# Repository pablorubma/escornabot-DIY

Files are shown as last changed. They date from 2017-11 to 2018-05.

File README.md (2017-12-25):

# AVISO!! En construcción, estos días retocaré muchas cosas aunque lo esencial siempre lo tendrás a mano :P
  
# Escornabot DIY  
  
Material recopilado de [Xoan Sampaiño](https://github.com/xoan), [Rafa Couto](https://github.com/rafacouto), [XDeSIG](https://github.com/xdesig), [Jorge Lobo Martínez](https://github.com/lobotic) y [mgesteiro](https://github.com/mgesteiro)   
  
Web oficial del robot escornabot http://escornabot.com

Vamos a describir uno tras otros todos los pasos a seguir para montar la versión DIY (la de los cablecicos)

# 1. Piezas Impresas3D Necesarias
  
Descripción         | imagen          | archivo         
------------- | ------------- | ------------- 
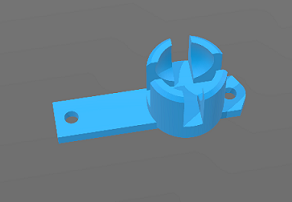
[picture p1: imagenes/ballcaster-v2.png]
ballcaster-v2.stl
Sujeción bola v2| | [ballcaster-v2.stl](archivos-stl/ballcaster-v2.stl)  
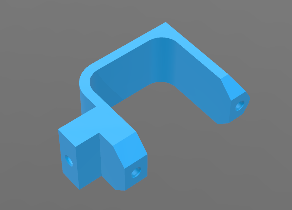
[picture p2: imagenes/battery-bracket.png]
battery-bracket.stl
Sujeción batería| | [battery-bracket.stl](archivos-stl/battery-bracket.stl)  
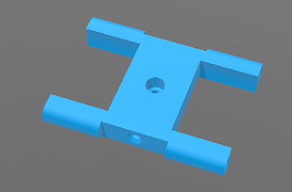
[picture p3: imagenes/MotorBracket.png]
MotorBracket.stl
Sujeción motores| | [MotorBracket.stl](archivos-stl/MotorBracket.stl)  
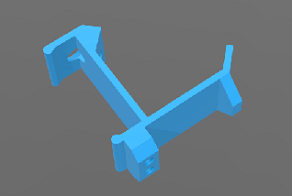
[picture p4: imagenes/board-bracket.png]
board-bracket.stl
Sujeción protoboard 170 puntos| | [board-bracket.stl](archivos-stl/board-bracket.stl)  
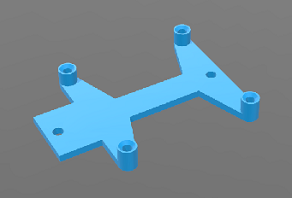
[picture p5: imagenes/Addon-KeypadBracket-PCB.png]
Addon-KeypadBracket-PCB.stl
Sujeción placa botonera| | [Addon-KeypadBracket-PCB.stl](archivos-stl/Addon-KeypadBracket-PCB.stl)  
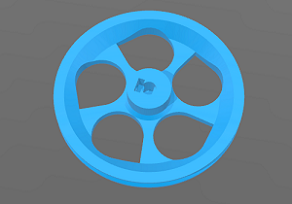
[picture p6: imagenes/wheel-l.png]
wheel-l.stl
Rueda izquierda| | [wheel-l.stl](archivos-stl/wheel-l.stl)  
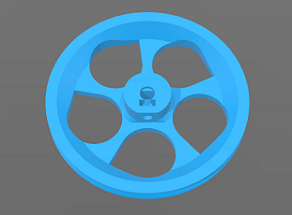
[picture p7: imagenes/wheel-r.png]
wheel-r.stl
Rueda derecha| | [wheel-r.stl](archivos-stl/wheel-r.stl)  

### 1.1 Opcional
  
En mi caso, no monto la pieza "sujeción interruptor". Dejo los cables para conectar macho con hembra y enseñar a los peques la conexión de los cables.

Descripción         | Imagen          | Archivo          
------------- | ------------- | ------------- 
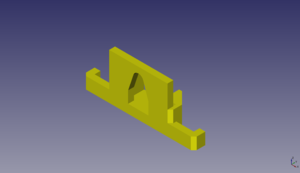
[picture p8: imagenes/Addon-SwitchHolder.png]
Addon-SwitchHolder.stl
Sujeción interruptor| | [Addon-SwitchHolder.stl](archivos-stl/Addon-SwitchHolder.stl)

# 2. Componentes Electrónicos
  
## 2.1. Placa Botonera 

Es la parte más problemática y tienes dos opciones:

### 2.1.1. Placa original totalmente artesanal

Tienes todos los detalles en la web del proyecto [pincha aquí](https://escornabot.com/web/es/content/botonera-audaciuso) 

Placa Original

También la tienes documentada en la  [guía del CFR Ferrol](https://www.edu.xunta.gal/centros/cfrferrol/aulavirtual2/pluginfile.php/18631/mod_resource/content/0/doc/Proxecto_K-KuriBOT_CFR_FERROL.pdf)

### 2.1.2. Versión de [XDeSIG](https://github.com/xdesig)
  
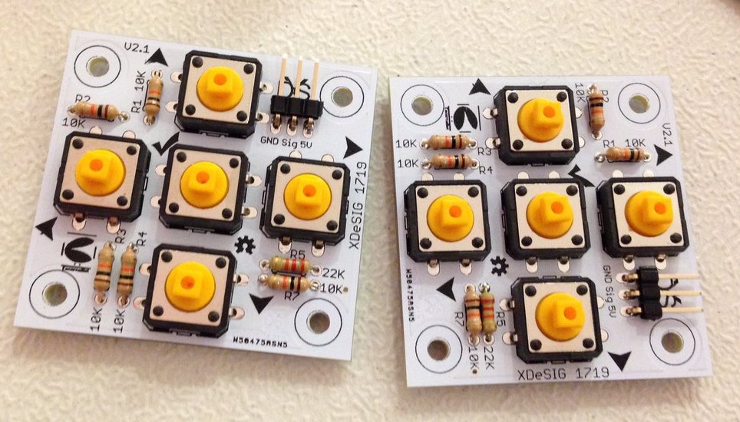
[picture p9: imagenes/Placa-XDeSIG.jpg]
Placa XDeSIG

  
La puedes pedir aquí - [Placa XDeSIG en PCBWay](https://www.pcbway.com/project/shareproject/W50475ASN5_Escorna_bot_2_1_Gerber.html)

Estos son los materiales que necesitas soldar en la placa:

- 5 resistencias 10k
- 1 resistencia 22k
- Pines acodados
- 5 botones 12mm (también puedes poner los pequeños)

### Para esta placa necesitas imprimir una sujeción concreta
  
También tiene carcasa :)
  
Descripción         | Imagen          | Archivo          
------------- | ------------- | ------------- 
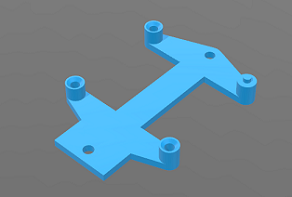
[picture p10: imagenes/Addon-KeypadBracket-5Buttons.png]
Addon-KeypadBracket-5Buttons.stl
Sujeción placa botonera XDeSIG| | [Addon-KeypadBracket-5Buttons.stl](archivos-stl/Addon-KeypadBracket-5Buttons.stl)
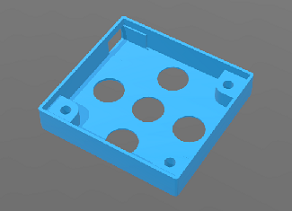
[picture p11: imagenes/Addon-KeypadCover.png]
Addon-KeypadCover.stl
Cubierta botonera XDeSIG| | [Addon-KeypadCover.stl](archivos-stl/Addon-KeypadCover.stl)
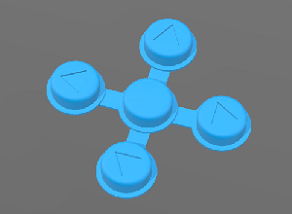
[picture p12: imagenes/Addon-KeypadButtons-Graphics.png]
Addon-KeypadButtons-Graphics.stl
Botones XDeSIG| | [Addon-KeypadButtons-Graphics.stl](archivos-stl/Addon-KeypadButtons-Graphics.stl)
  
__*Recuerda, una vez montada tienes que [comprobar y configurar las lecturas de la botonera](https://escornabot.com/web/es/content/comprobacion-y-configuracion-de-las-lecturas-de-botonera)__

## 2.2. Componentes del cuerpo 

2 – Motores paso a paso **28BY J-48** con “placa” **drive ULN2003**  
2 – Juntas tóricas de **63x60x3** (para las ruedas)  
1 – **Arduino Nano Atmega328** (También puedes usar un Arduino Pro-Mini)  
1 – Zumbador o **Buzzer de 5V**  
1 – **Protoboard** pequeña de **170 puntos**  
1 – **Portapilas** de cuatro unidades para **pilas AA** (no confundir con las AAA que son las finitas)  
20 – Cables arduino macho-hembra (te van a sobrar pero más vale prevenir)  
2 – Cables arduino macho-macho (para la conexión pilas-protoboard)  
16 – Tornillos M3 (a mi me gustan con la punta para destornillador de estrella)  
2 – Tuercas M3 (para las ruedas)  
1 – **Canica de 14mm** (si te gustan las de la carita, busca “bola 14mm smile”)  
  
Si eres curios@ y quieres comprarlos por tu cuenta estoy creando una [lista de componentes](https://github.com/pablorubma/escornabot-DIY/tree/master/componentes)

# 3. Montaje del cuerpo

Puedes consultar la [guía de montaje en la página oficial](https://escornabot.org/wiki/index.php/Gu%C3%ADa_de_montaje_(Brivoi)).

También te sirve de ayuda si montas la [versión Ogaki de abiertocc](https://abierto.cc/shop/#search=ogaki) o la [versión v2.12](https://twitter.com/i/moments/924502947236601856)  

# 4. Cableado de los drivers, buzzer y portapilas

Ya tenemos todo colocado en su sitio, ahora hay que conectar los diferentes componentes con Arduino NANO. Para eso puedes seguir la [guía de cableado](https://escornabot.com/web/es/content/cableado)

# 5. Instalación IDE Arduino y descarga de la programación

Si es la primera vez que utilizas Arduino lo mejor es consultar directamente en la web, [instalar el software (IDE) de arduino](https://www.arduino.cc/en/Guide/Windows)

Las diferentes programaciones las puedes encontrar en el [repositorio de Rafa Couto en GitHub](https://github.com/escornabot/arduino/releases/tag/v1.4.1)

Algunas cosas importantes que debes seleccionar antes de compilar y cargar la programación en tu arduino NANO:

* Selecciona la **placa Arduino NANO** (o la que uses)
* El **procesador** que usa (si es el 164 o 328)
* **Puerto COM del PC** al que lo tienes conectado

# 6. Comprobación de la botonera

Ya lo he comentado antes, pero **este paso se suele olvidar** y **es uno de los que más quebraderos de cabeza causa**. Yo hago la comprobación una vez montado el robot entero, pero tu puedes hacerlo cuando quieras.

[Comprobación y configuración de las lecturas de la botonera](https://escornabot.com/web/es/content/comprobacion-y-configuracion-de-las-lecturas-de-botonera)

Anota los valores de cada botón para editarlos en el archivo **configuration.h**

# 7. A jugar

Si todo ha ido bien, el pequeñajo tiene que empezar a caminar. Cuando te familiarices un poco con Arduino puedes probar a tocar la programación, cambiar los giros, la velocidad, los sonidos del buzzer, añadir sensores, ponerle bluethoot, wifi y todo lo que se te ocurra.

A continuación tienes unos recursos extra :)

# Bluetooth y manejo mediante app android [Jorge Lobo Martínez](https://github.com/lobotic)
  
Puedes ponerle Bluetooth a tu escornabot. Solo necesitas leer el artículo de Jorge en su blog https://ceipmiskatonic.blogspot.com.es/2015/07/usando-el-escornabot-por-bt.html

# MUWI uso mediante Wifi con módulo ESP-01 [mgesteiro](https://github.com/mgesteiro) 
  
Con la placa escornabot v 2.12 va muy bien, con la versión DIY todavía no he probado.

De todos modos, os dejo el enlace al repositorio de Miguel donde podeis encontrar toda la información para que lo tengáis a mano. https://github.com/escornabot/esp-muwi

# Guías y manuales
  
Guía de montaje del CFR Ferrol, es en la que me basé para montar mi primer escornabot. Tienes instrucciones detalladas para montar la botonera - [Guía montaje CFR Ferrol](https://www.edu.xunta.gal/centros/cfrferrol/aulavirtual2/pluginfile.php/18631/mod_resource/content/0/doc/Proxecto_K-KuriBOT_CFR_FERROL.pdf)

Listado completo de materiales necesarios, web original escornabot. Todos los componentes que te haran falta para poner al pequeñajo a caminar - [Listado materiales](http://escornabot.org/wiki/index.php/Lista_de_materiales_(Brivoi))

Guía de montaje sin incluir ensamblaje de botonera, web original escornabot - [Guía montaje](http://escornabot.org/wiki/index.php/Gu%C3%ADa_de_montaje_(Brivoi))

Como comprobar la lectura de la botonera para luego modificar los valores en el archivo "configuration.h" - [Comprobación botonera](https://escornabot.com/web/es/content/comprobacion-y-configuracion-de-las-lecturas-de-botonera)

Diferentes versiones de Rafa Couto realizadas hasta ahora [Versiones arduino para escornabot](https://github.com/escornabot/arduino/releases)  

# Recursos y materiales

En la wiki del proyecto oficial tienes un apartado dedicado a recursos donde puedes encontrar actividades o tableros para escornabot [Recursos Wiki Oficial](http://escornabot.org/wiki/index.php/Recursos)
  
Un imprescindible es el Blog de [Jorge Lobo Martínez](https://github.com/lobotic), donde comparte las actividades que hace en clase. Te dejo enlace a la sección donde trata cosas de escornabot pero revisa el blog completo porque mola mucho - [Blog Lobotic](http://ceipmiskatonic.blogspot.com.es/search/label/Escornabot)
  
Puedes disfrazar a tu pequeñajo [Disfraz Escornabot](https://github.com/pablorubma/escornabot-DIY/tree/master/disfraces)

# Para solucionar dudas y problemas

Si tienes cualquier duda puedes abrir un tema en el grupo creado en google y entre todos te ayudaremos :)
https://groups.google.com/forum/#!forum/escornabot_users

## Bienvenid@ al lado escornabot de la fuerza muahahaha

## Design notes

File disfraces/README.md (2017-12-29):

# Quiero mi disfraz!!

El origen de todo esto viene de [@mininacheshire](https://twitter.com/escornabot/status/568520109033009152) y del [blog de Lobotic](http://ceipmiskatonic.blogspot.com.es/2016/01/disfraces-para-escornabot-brivoi.html)

# Material necesario
* Goma eva
* Tijeras o cuter
* Regla
* Pegamento
* Folios
* Pinturas
* Ojos molones
* Cualquier objeto que resulte útil
  
## Manos a la obra
Un A3 de goma eva mide 30cm de ancho y da de sobra para cubrir el robot de lado a lado. Los 42 cm de largo permite cortar 6 tiras de 7 cm en cada plancha. Yo hago los cortes con cúter, pero si van a trabajar los peques con tijeras mucho mejor 🙂

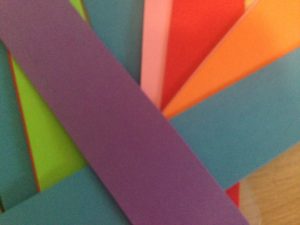
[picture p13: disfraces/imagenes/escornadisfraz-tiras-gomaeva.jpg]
escornadisfraz-tiras-gomaeva


# Disfrazando la versión DIY
Para simplificar usaremos las piezas para fijar el disfraz, en concreto la bola y la placa.
  
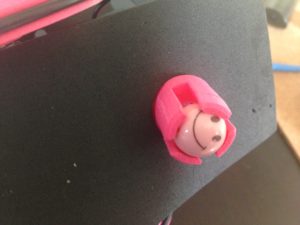
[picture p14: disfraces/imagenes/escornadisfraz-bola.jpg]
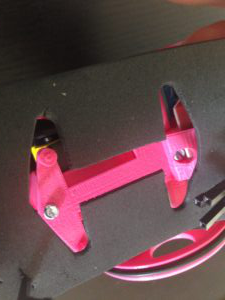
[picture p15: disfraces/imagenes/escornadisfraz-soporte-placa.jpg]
 
  
Las propias piezas nos van a servir de plantilla para cortar su silueta. Colocando la tira sobre el robot puedes calcular donde quieres que quede la tira, en mi caso los puse para que se quedara el corte en la parte de la bola:
  
## Cableado
Haremos unos agujeros para pasar los cables de las baterías y los que conectan a la placa.
  
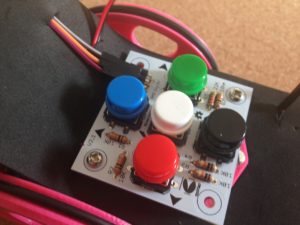
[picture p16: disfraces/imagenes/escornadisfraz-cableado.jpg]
escornadisfraz-cableado
  
  
## Buzzer o altavoz
El buzzer o zumbador lo podemos pinchar directamente en la plancha y utilizarlo de nariz.  Por la parte trasera se conectan los cables sin problema quedando bastante sujeto.
  
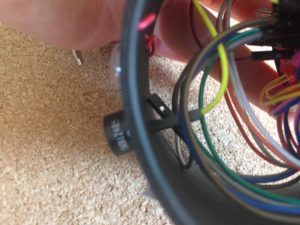
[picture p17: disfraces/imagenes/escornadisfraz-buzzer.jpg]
escornadisfraz-buzzer
  
  
## Ojos
Yo no puedo evitar usar estos ojos pero cada uno debe utilizar su imaginación. Para las cejas he utilizado el mismo cable de arduino haciendo dos agujeros donde anclar los extremos, después puedes darle la forma que quieras.
  
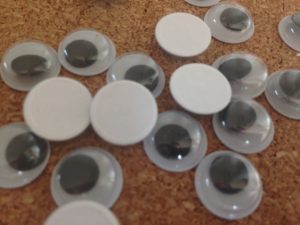
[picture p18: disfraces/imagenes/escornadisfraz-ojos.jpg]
escornadisfraz-ojos
  
    
## Boca
Buscando un poco por Internet tienes un montón de imágenes con bocas para imprimir, recortar y pegar.
  
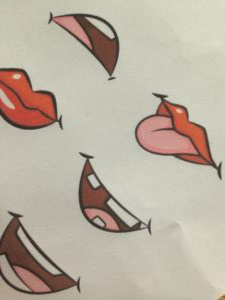
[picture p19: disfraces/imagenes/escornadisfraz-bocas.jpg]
escornadisfraz-bocas
  
    
## Cuerpo
Utiliza trozos de goma eva para adornar el cuerpo, folios pintados o cualquier objeto que puedas pegar y quede molón.
  
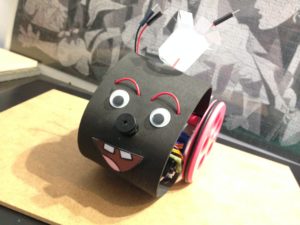
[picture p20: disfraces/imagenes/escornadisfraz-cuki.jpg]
escornadisfraz-cuki
  
    
# Disfrazando la versión 2.12
En este caso hay que tener en cuenta que la placa es rectangular y más grandota. Como en la anterior uso las propias piezas para anclar la goma eva.
  
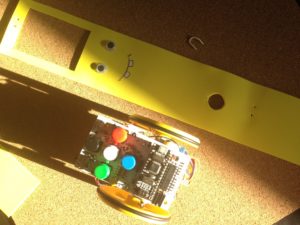
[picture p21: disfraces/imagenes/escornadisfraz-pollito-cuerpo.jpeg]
escornadisfraz-pollito-cuerpo
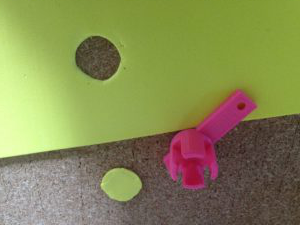
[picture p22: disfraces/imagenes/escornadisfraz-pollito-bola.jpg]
escornadisfraz-pollito-bola
   
    
Al no tener cables necesitas menos trozo de largo para cubrir el robot entero. Yo he utilizado ese sobrante para fabricarle una colita usando un cable como fijación para poder quitar y poner con facilidad.
  
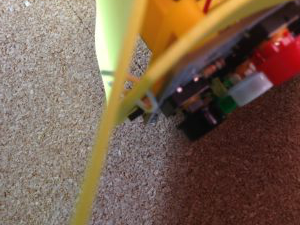
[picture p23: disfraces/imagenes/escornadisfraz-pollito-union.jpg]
escornadisfraz-pollito-union
  
    
Ya tienes una base sobre la que trabajar, ahora imaginación al poder.
  
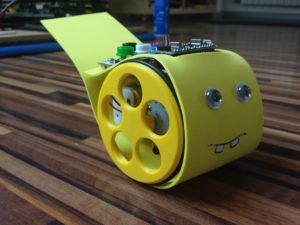
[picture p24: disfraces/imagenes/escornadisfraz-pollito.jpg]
escornadisfraz-pollito
  
    
# Otros ejemplos
En la wiki oficial tienes muchos ejemplos que te pueden dar ideas, te dejo enlace a [máscaras Escornabot](http://escornabot.org/wiki/index.php/Recursos#M.C3.A1scaras)

También este video de Youtube del [CEIP Avion](https://www.youtube.com/watch?v=MtaqqE0XVQg)

O este otro de [Jorge Alba](https://twitter.com/_jorgealba/status/941775330112614401)

# Caretas [Lobotic](https://github.com/lobotic/Escornabot/tree/master/3D) para impresión 3D

[Elefante](https://www.thingiverse.com/thing:2722321)  
[león](https://www.thingiverse.com/thing:2731368)  
[Mono](https://www.thingiverse.com/thing:2735957)  
  
Prueba, juega, crea y sobre todo…
  
# Comparte tu disfraz!

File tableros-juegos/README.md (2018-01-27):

# Material didáctico para usar con [escornabot](http://escornabot.com)

Material recopilado de la [wiki oficial](http://escornabot.org/wiki/index.php/Recursos)

# Tableros  

## Tablero casillas blancas y oficial escornabot

El tablero con casillas blancas es muy interesante si le ponemos bolsas tipo zip cortadas en cada casilla y las utilizamos para meter tarjetas personalizadas.

Tienes en la parte inferior las tarjetas con recorridos, recortadas van eligiendo al azar un recorrido.

Tablero A-3         | Archivo SVG          | Archivo PDF         
------------- | ------------- | -------------              
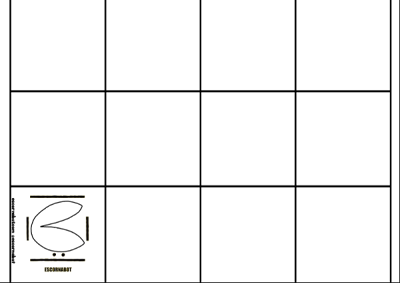
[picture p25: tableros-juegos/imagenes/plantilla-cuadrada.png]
  | [Plantilla cuadrados formato .SVG](https://drive.google.com/file/d/0B32DBGno8hnobk51LXhJUHp0Vlk/view) | [Plantilla cuadrados formato .PDF](https://drive.google.com/file/d/0B32DBGno8hnodjZWVXVJTGdiY0k/view)  
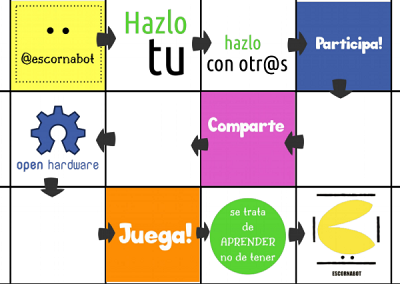
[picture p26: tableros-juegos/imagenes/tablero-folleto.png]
 | [Tablero folleto formato .SVG](https://drive.google.com/file/d/0B32DBGno8hnoeld1VlFjakIzUFE/view?usp=drive_web) | [Tablero folleto formato .PDF](https://drive.google.com/file/d/0B32DBGno8hnoM1pBOEhCa0lFTjg/view) 

## Tablero números

Puedes jugar tirando un dado y que busquen la casilla, realizando sumas simples... Edita el tablero para complicarlo.

Otro juego divertido son las carreras. Es para dos personas, cada uno con un escornabot y fuera del tablero. Se lanza un dado, como los números se repiten el objetivo es que alcancen la primera casilla que vean.

Tablero A-3         | Archivo SVG          | Archivo PDF         
------------- | ------------- | -------------   
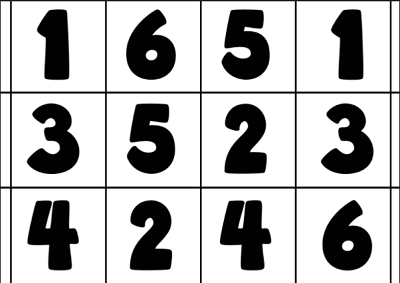
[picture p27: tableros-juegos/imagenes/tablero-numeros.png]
 | [Tablero Números formato .SVG](https://drive.google.com/file/d/0B32DBGno8hnoTDlCNWl0N3ZRdGc/view) | [Tablero Números formato .PDF](https://drive.google.com/file/d/0B0UX14YozB7jTno0dTlkeHpnVVFTNGMzaFpuelZmNlhidkNF/view) 

## Tablero condicional

Se debe llegar desde la casilla inferior izquierda con el triángulo verde hasta la casilla inferior derecha cumpliendo las condiciones de las casillas. La casilla con el aspa roja no se puede pisar, del mismo modo que la azul ya que se caería al agua.

Tablero A-3         | Archivo SVG          | Archivo PDF         
------------- | ------------- | -------------   
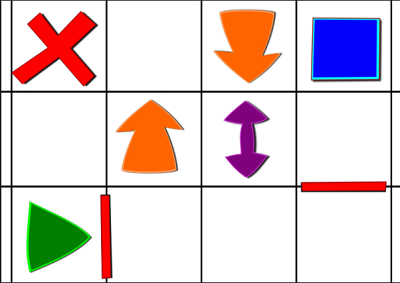
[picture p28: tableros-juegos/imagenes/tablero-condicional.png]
 | [Tablero condicional formato .SVG](https://drive.google.com/file/d/0B32DBGno8hnocW1KQ2dnUHFKVzg/view) | [Tablero condicional formato .PDF](https://drive.google.com/file/d/0B32DBGno8hnoalZfUDlqZjEya1U/view)  

## Tablero figuras geométricas

Se pueden recortar las figuras interiores o cambiar de color para que l@s peques primero hagan la composición del tablero, luego juegan combinando colores y formas geométricas. Puedes crear dos dados, uno contiene colores y otro las formas geométricas.

Tablero A-3         | Archivo SVG          | Archivo PDF         
------------- | ------------- | -------------   
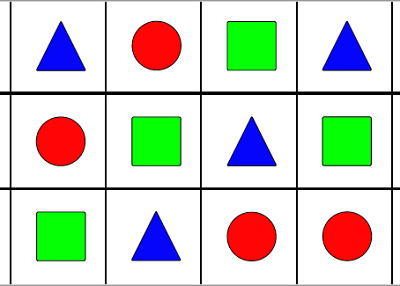
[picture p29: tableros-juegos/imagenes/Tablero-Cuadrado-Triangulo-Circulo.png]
  | [Tablero-Cuadrado-Triangulo-Circulo.svg](archivos/Tablero-Cuadrado-Triangulo-Circulo.svg) | [Tablero-Cuadrado-Triangulo-Circulo.pdf](archivos/Tablero-Cuadrado-Triangulo-Circulo.pdf)  

## Tableros alfabeto

Para trabajar las letras con animalicos :)

Tablero A-3         | Archivo SVG          | Archivo PDF         
------------- | ------------- | -------------   
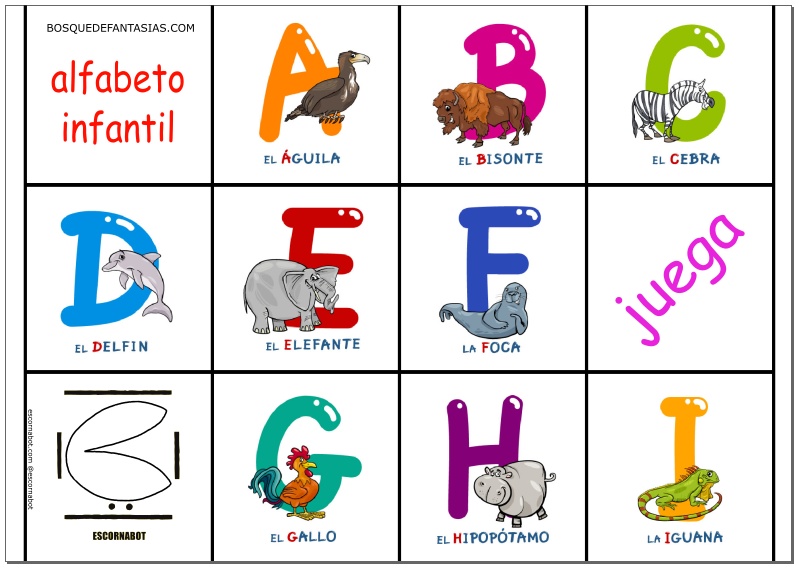
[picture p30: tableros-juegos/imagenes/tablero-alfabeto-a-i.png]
  | [tablero-alfabeto-a-i.svg](archivos/tablero-alfabeto-a-i.svg) | [tablero-alfabeto-a-i.pdf](archivos/tablero-alfabeto-a-i.pdf)  
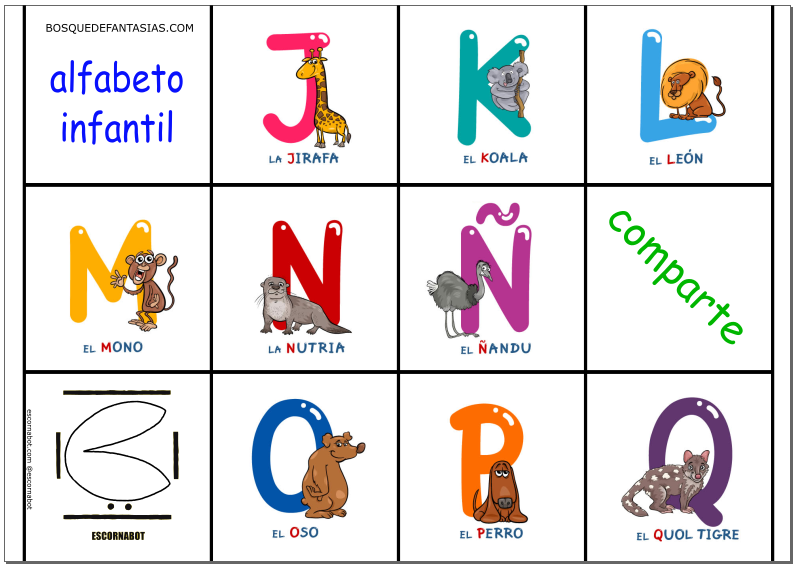
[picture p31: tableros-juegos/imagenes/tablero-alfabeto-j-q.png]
  | [tablero-alfabeto-j-q.svg](archivos/tablero-alfabeto-j-q.svg) | [tablero-alfabeto-j-q.pdf](archivos/tablero-alfabeto-j-q.pdf)  
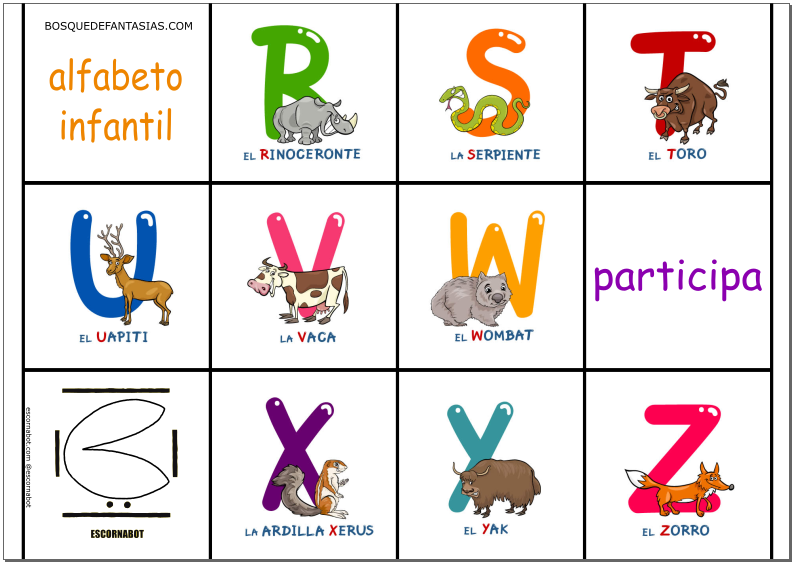
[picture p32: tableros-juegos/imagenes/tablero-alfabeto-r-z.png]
  | [tablero-alfabeto-r-z.svg](archivos/tablero-alfabeto-r-z.svg) | [tablero-alfabeto-r-z.pdf](archivos/tablero-alfabeto-r-z.pdf)  

## Tablero triangular

Tablero A-3         | Archivo SVG          | Archivo PDF         
------------- | ------------- | -------------   
Para usar la plantilla triangular debes cambiar la programación para que los grados en los giros se adapten al dibujo, el robot debe ir por las líneas y llegar a los vértices de los triángulos

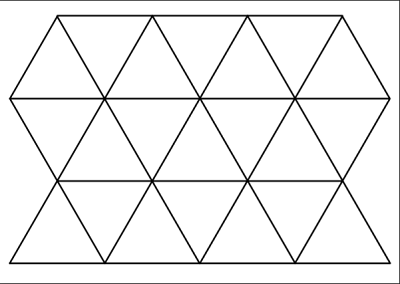
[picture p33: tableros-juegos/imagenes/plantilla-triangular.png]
  | [Plantilla triangular formato .SVG](https://drive.google.com/file/d/0B32DBGno8hnoSEkyN3VRM1I0Rmc/view) | [Plantilla triangular formato .PDF](https://drive.google.com/file/d/0B32DBGno8hnod1pXVzdfVG54VnM/view)  

## Tablero escritores gallegos
  
Tableros A-4         | Archivo SVG          | Archivo PDF         
------------- | ------------- | -------------       
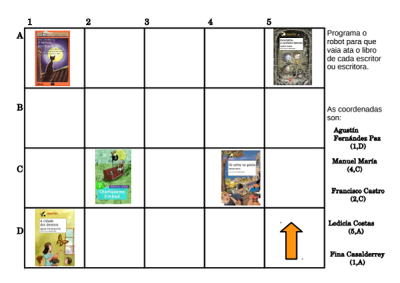
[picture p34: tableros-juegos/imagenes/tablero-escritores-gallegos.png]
 | | [Tablero escritores gallegos formato .PDF](https://drive.google.com/file/d/0B5m90BTAG1QYSExtNWdBNjVuU0E/view)  

## Tarjetas

Tarjeta         | Archivo            
------------- | -------------       
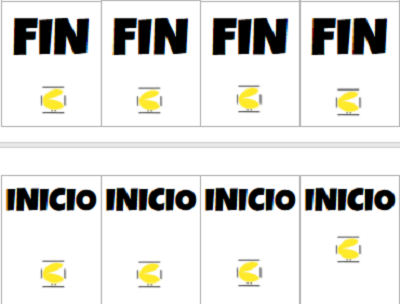
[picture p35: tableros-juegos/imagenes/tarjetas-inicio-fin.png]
 | [Tarjetas inicio-fin formato Word](https://docs.google.com/document/d/12gfkgnx5Rgb8NKzSXDHQ7-2KmUop8931cPN26ciuWcE/edit) 
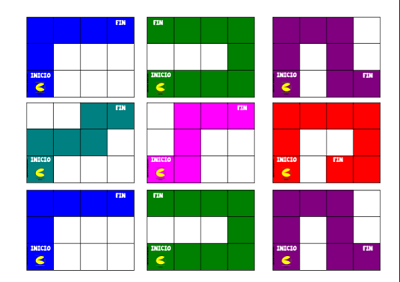
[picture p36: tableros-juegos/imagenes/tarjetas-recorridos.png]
 | [Tarjetas recorridos formato .PDF](https://drive.google.com/file/d/0B0UX14YozB7jTGZ3d1dYSGNsSkJZU0Fqd1BTMjJCMWdHVGRB/view) 
 | [Tarjetas frutas formato Word](https://docs.google.com/document/d/1xnoPbf6wEXKz65S-1-KflOl4RJz2JpOLmkt9J7G1E6k/edit)  
 | [Tarjetas ecosistemas formato .PDF](http://escornabot.org/wiki/images/f/f7/Ecosistemas.pdf)
  
## Dados

[Cuerpos Geométricos para utilizar como dados](https://drive.google.com/file/d/0B0UX14YozB7jc0IyU1Rfb01kR3M/view)

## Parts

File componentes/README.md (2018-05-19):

### IMPORTANTE - Cada uno es responsable de lo que compre esto simplemente es una orientación

## Teneis los componentes necesarios para montar un escornabot en el [repositorio version DIY](https://github.com/pablorubma/escornabot-DIY/blob/master/README.md)

2 – Motores paso a paso 28BY J-48 con “placa” drive ULN2003  
2 – Juntas tóricas de 63x57x3 (para las ruedas)  
1 – Arduino Nano Atmega328 (También puedes usar un Arduino Pro-Mini)  
1 – Zumbador o Buzzer de 5V  
1 – Protoboard pequeña de 170 puntos  
1 – Portapilas de cuatro unidades para pilas AA (no confundir con las AAA que son las finitas)  
20 – Cables arduino macho-hembra (te van a sobrar pero más vale prevenir)  
2 – Cables arduino macho-macho (para la conexión pilas-protoboard)  
16 – Tornillos M3 (a mi me gustan con la punta para destornillador de estrella)  
2 – Tuercas M3 (para las ruedas)  
1 – Canica de 14mm (si te gustan las de la carita, busca “bola 14mm smile”)  

Voy a compartir donde poder adquirir estos componentes y los días que van tardando en llegar.  

*Los días son orientativos, pueden variar. China es así.

# Componentes cuerpo
  
14 días - [Motor 28BYJ-48 + ULN2003 ](https://es.aliexpress.com/item/Frees-hipping-5V-4-Phase-Stepper-Step-Motor-Driver-Board-ULN2003-with-drive-Test-Module-Machinery/32706559510.html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)  
28 días - [Junta tórica 63x57x3mm](https://es.aliexpress.com/item/Electronic-Component-Red-O-Ring-62mm-x-56mm-x-3mm-O-Ring-Washer-Seals-Assortment/32371865042.html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). Gracias a [CMasso](https://twitter.com/CMasso_Robbie)  
18 días - [Arduino NANO Atmega328](https://es.aliexpress.com/item/Nano-V3-ATmega328-CH340G-Micro-USB-Pin-headers-NOT-soldered-Compatible-for-Arduino-Nano-V3-0/32664577152.html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)  
24 días - [Buzzer 5V](https://es.aliexpress.com/item/Free-Shipping-10pcs-Electromagnetic-buzzer-5V-5V-active-buzzer/635190995.html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)  
14 días - [Protoboard 170 puntos](https://es.aliexpress.com/item/Free-Shipping-wholesale-1pcs-lot-SYB-170-Mini-Solderless-Prototype-Experiment-Test-Breadboard-170-Tie-points/32348752975.html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)  
14 días - [Portapilas 4 x Pilas AA](https://es.aliexpress.com/item/MOSUNX-Futural-Digital-2-slot-4-x-AA-Battery-Back-To-Back-Holder-Case-Box-With/32804061860.html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)  
24 días - [Calbe Arduino 10cm Macho-Hembra](https://es.aliexpress.com/item/40pcs-lot-10cm-40P-2-54mm-dupont-cable-jumper-wire-dupont-line-male-to-female-dupont/32674901253.html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)  
24 días - [Cable Arduino 10cm Macho-Macho](https://es.aliexpress.com/item/Free-shipping-Dupont-line-40pcs-10cm-male-to-male-jumper-wire-Dupont-cable-breadboard-cable-jump/32700513558.html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)  
14 días - [Tornillos M3 de 10mm](https://es.aliexpress.com/item/F85-100pcs-Metric-M3-x-10mm-Phillips-Pan-Head-Screws-Stainless-Steel/32599665025.html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)  
14 días - [Tuercas M3 de 10mm](https://es.aliexpress.com/item/100pcs-lot-M3-Screw-Nut-Hex-Nuts-Hexagonal-3mm-For-Coupler-Motor-Mount-Servo-Bracket-Robot/32815312449.html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)  
18 días - [Bolas 14mm Smile](https://es.aliexpress.com/item/40-pcs-14mm-Mixed-Smiling-Face-Smile-Round-Ball-Spacer-Beads-Plastic-Acrylic-For-DIY-Necklace/32699472196.html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)  
14 días - [Tornillos M3 de 5mm (un poco mas cortos para poner en drivers o botonera)](https://es.aliexpress.com/item/F85-100pcs-Metric-M3x5mm-Phillips-Pan-Head-Screw-for-2-5-HDD-SSD-DVD-ROM-Motherboard/32599458544.html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)  

# Componentes para placa botonera

28 días - [PCB Diseñada por XDeSIG](https://www.pcbway.com/project/shareproject/W50475ASN5_Escorna_bot_2_1_Gerber.html)  
18 días - [Resistencias cerámicas 10k 1/4W 5%](https://es.aliexpress.com/item/1000pcs-Resistors-0-25watt-Carbon-Film-Resistor-10K-10KOHM-0-25W-1-4w-Resistance-SET-5/32424613090.html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)  
24 días - [Resistencias cerámicas 22k 1/4W 5%](https://es.aliexpress.com/item/Free-Shipping-1000pcs-Resistors-470-OHM-OHMS-1-4W-5-Carbon-Film/685770481.html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)  
24 días - [Pulsadores 12x12x7,3 con plástico colores (azul, blanco, rojo, verde y amarillo)](https://es.aliexpress.com/item/Free-shipping-100PCS-Tactile-Push-Button-Switch-Momentary-Tact-Cap-12-12-7-3MM-Micro-switch/32638121990.html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)  
28 días - [Pulsadores 12x12x7,3 con plástico colores (azul, blanco, rojo, verde y negro)](https://es.aliexpress.com/item/100pcs-Plastic-Tactile-Switch-PCB-Tact-Push-Button-Momentary-Switch-4-Pins-5-Color-Button-Cap/32826994795.html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)  
x días - [Pines acodados para los tres conectores](https://es.aliexpress.com/item/Hot-Sale-10pcs-40-Pin-1x40-Single-Row-Male-2-54mm-Breakable-Pin-Header-Right-Angle/32774385491.html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)

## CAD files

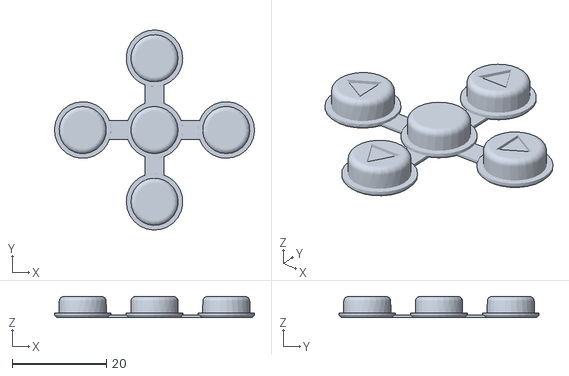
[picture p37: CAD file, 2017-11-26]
archivos-stl/Addon-KeypadButtons-Graphics.stl
42.5 x 42.5 x 4.50

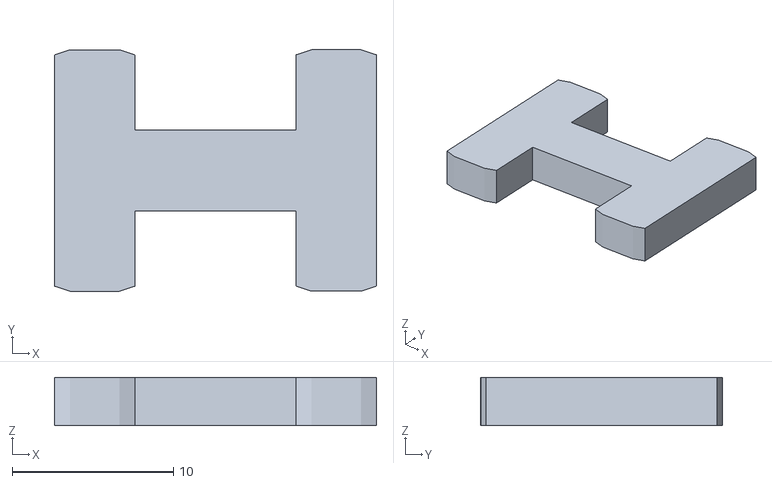
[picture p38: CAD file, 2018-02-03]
tableros-juegos/corte-laser/piezas-escornabot/Pieza-H.stl
20.0 x 15.0 x 3.00

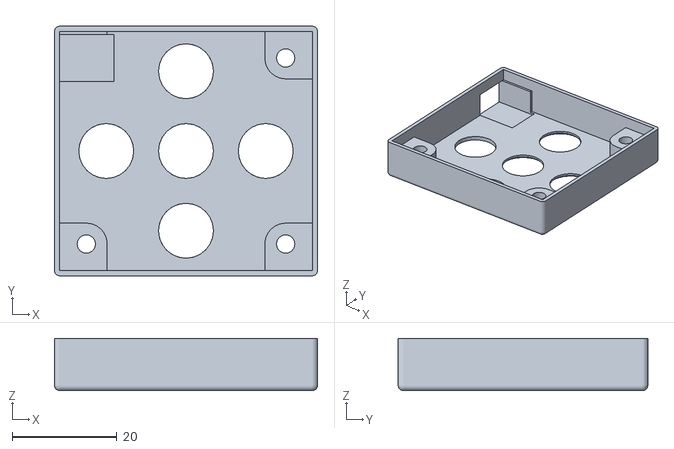
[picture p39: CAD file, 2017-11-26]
archivos-stl/Addon-KeypadCover.stl
50.3 x 47.7 x 10.0

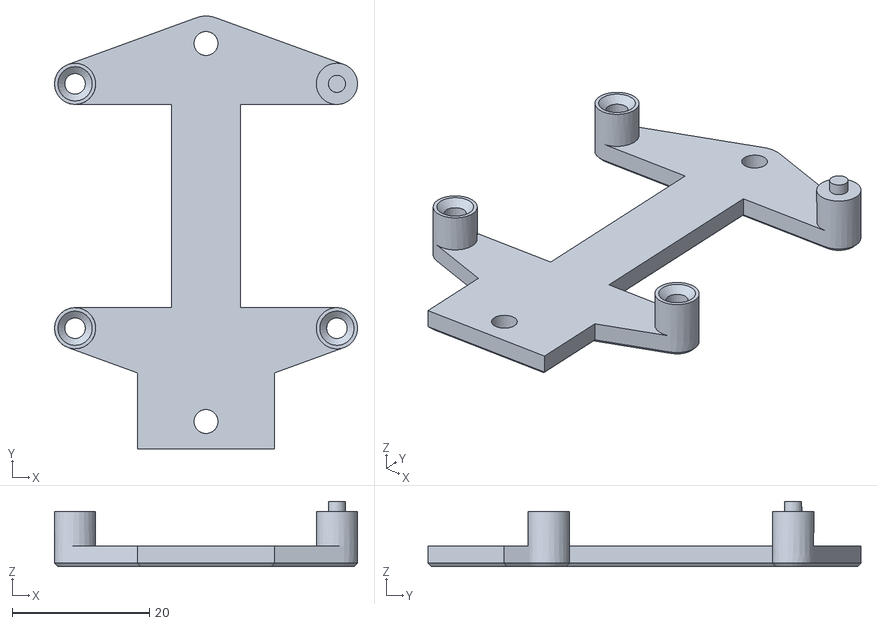
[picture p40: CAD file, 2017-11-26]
archivos-stl/Addon-KeypadBracket-5Buttons.stl
44.1 x 63.0 x 9.50

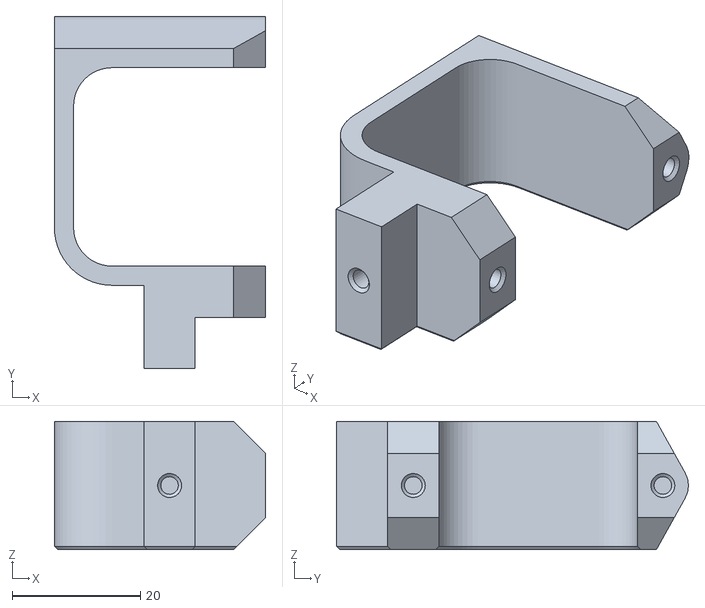
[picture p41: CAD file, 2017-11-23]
archivos-stl/battery-bracket.stl
33.0 x 55.0 x 20.0

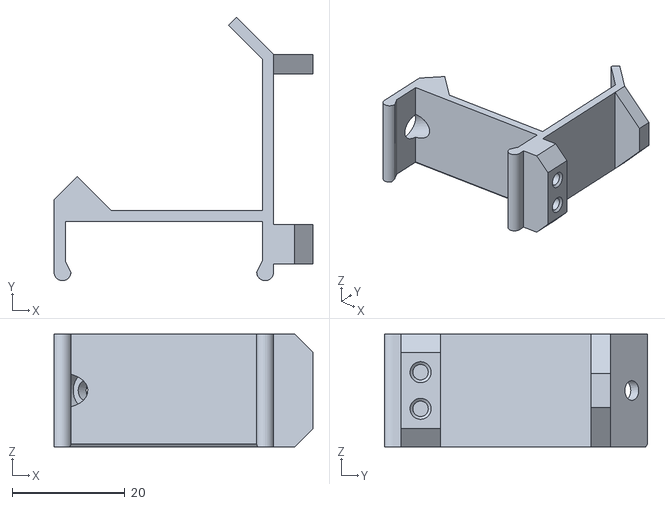
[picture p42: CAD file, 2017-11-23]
archivos-stl/board-bracket.stl
46.0 x 46.8 x 20.0

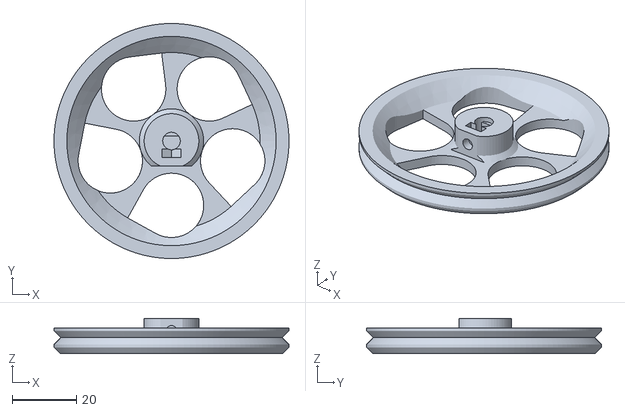
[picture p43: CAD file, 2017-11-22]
archivos-stl/wheel-r.stl
73.0 x 73.0 x 11.0

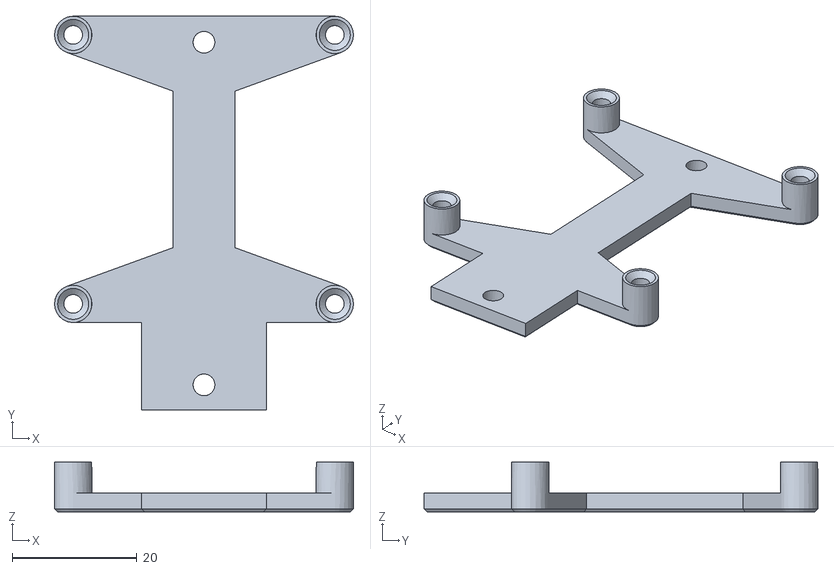
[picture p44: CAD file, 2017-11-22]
archivos-stl/Addon-KeypadBracket-PCB.stl
48.0 x 63.2 x 8.00

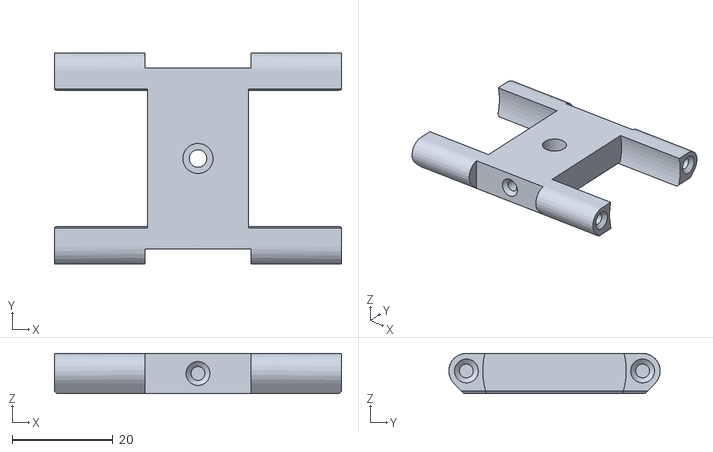
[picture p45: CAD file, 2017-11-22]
archivos-stl/MotorBracket.stl
57.0 x 42.0 x 8.00

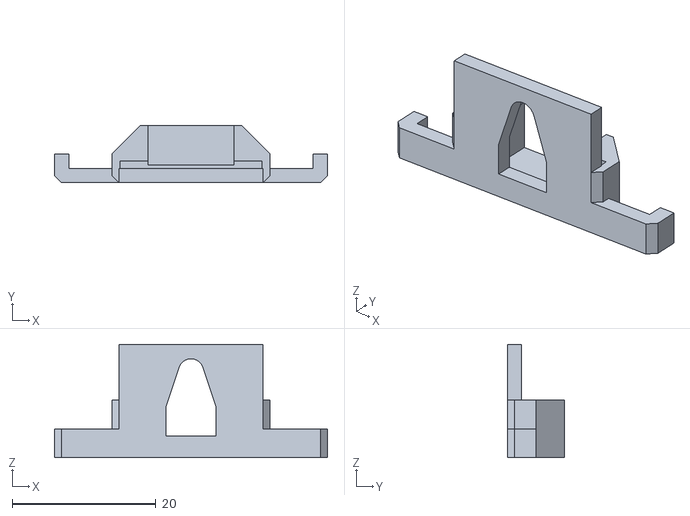
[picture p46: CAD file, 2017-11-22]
archivos-stl/Addon-SwitchHolder.stl
38.0 x 8.00 x 15.8

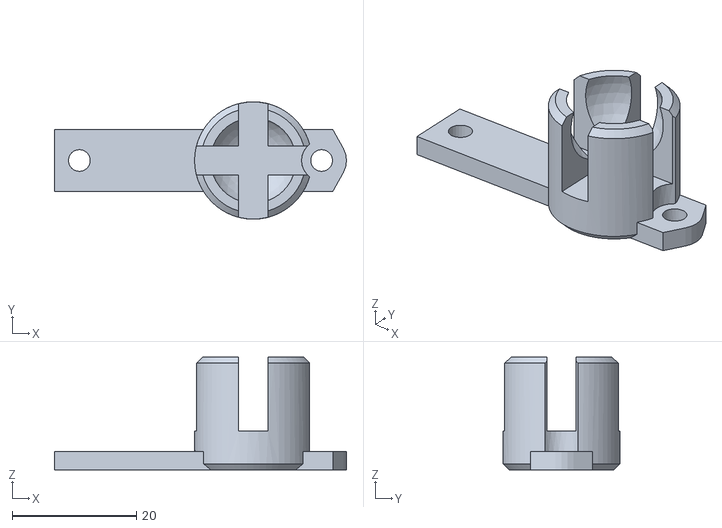
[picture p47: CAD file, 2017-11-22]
archivos-stl/ballcaster-v2.stl
47.0 x 18.9 x 18.2

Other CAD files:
archivos-stl/wheel-l.stl

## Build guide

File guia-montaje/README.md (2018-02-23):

# EN CONSTRUCCIÓN :)

# Basada en la [guía oficial](https://escornabot.org/wiki/index.php/Gu%C3%ADa_de_montaje_(Brivoi))

# Guía Montaje para la versión Escornabot DIY

Los componentes detallados los puedes encontrar [aquí](https://github.com/pablorubma/escornabot-DIY#22-componentes-del-cuerpo) y son estos:

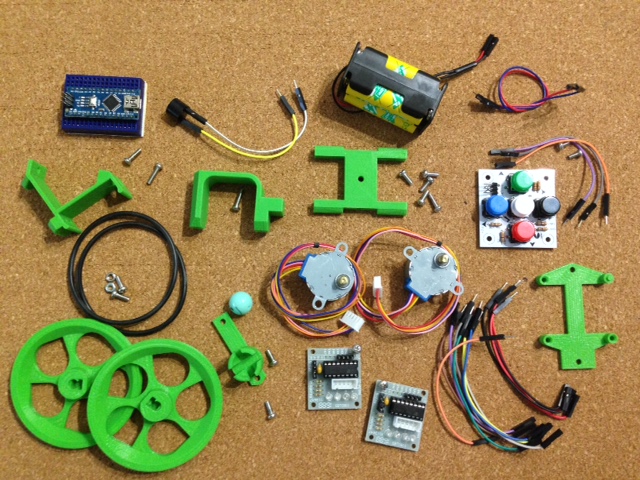
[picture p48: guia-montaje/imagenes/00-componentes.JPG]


## Ensamblaje motores

Material necesario:
* *Pieza "MotorBracket"*
* *2 Motores paso a paso 28BYJ-48 5V (solo los motores los drivers los usaremos más adelante)*
* *4 Tornillos M3 de 10mm*

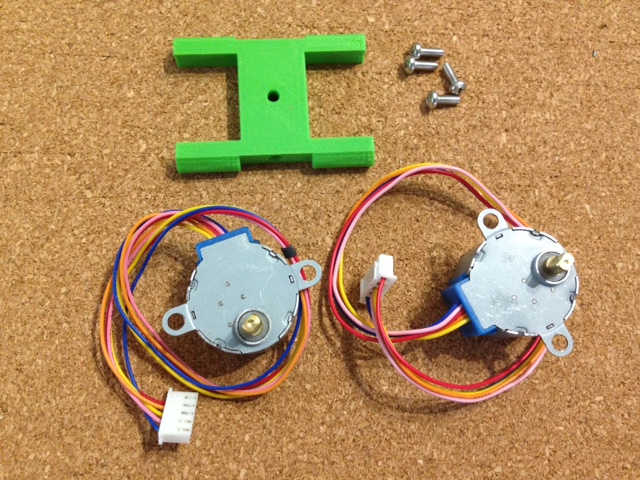
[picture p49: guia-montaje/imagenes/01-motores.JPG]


Dependiendo de la calidad de las piezas impresas este paso te costará más o menos.

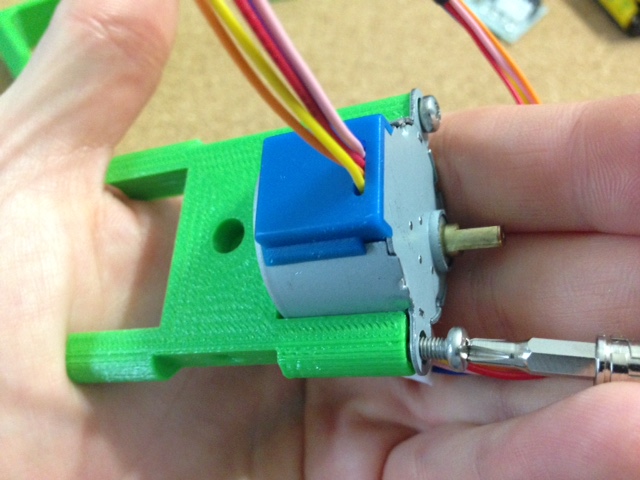
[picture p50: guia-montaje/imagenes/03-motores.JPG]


>__NOTA: Coloca los motores en la orientación que se muestra en la siguiente imagen, la zona azul en el mismo lado de la pieza donde el agujero central del tornillo tiene una muesca para encajar el tornillo.__

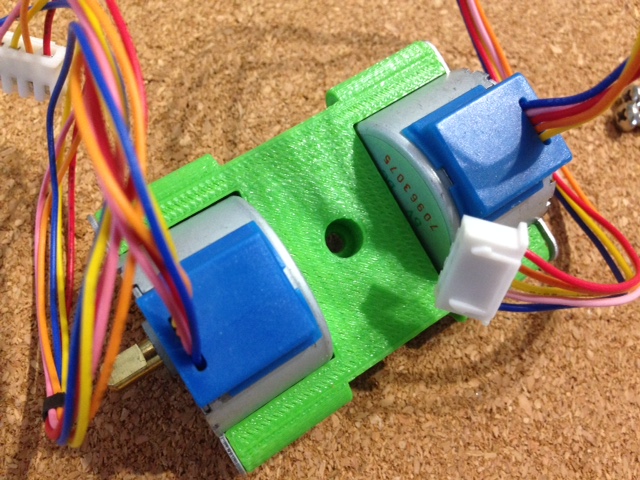
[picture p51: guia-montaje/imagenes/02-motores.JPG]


## Soporte portapilas-batería

Material necesario:
* *Pieza "battery-bracket"*
* *1 Tornillo M3 de 10mm*

>__NOTA: La pieza va colocada al lado contrario donde quedó la parte azul de los motores como puedes ver en las imágenes.__

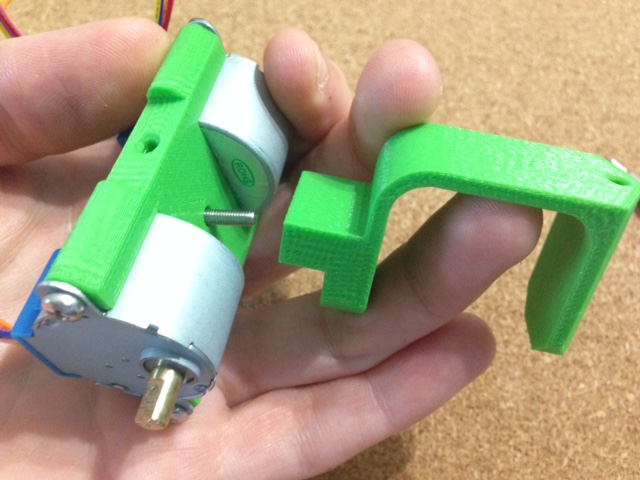
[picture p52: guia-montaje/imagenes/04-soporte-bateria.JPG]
04-soporte-bateria

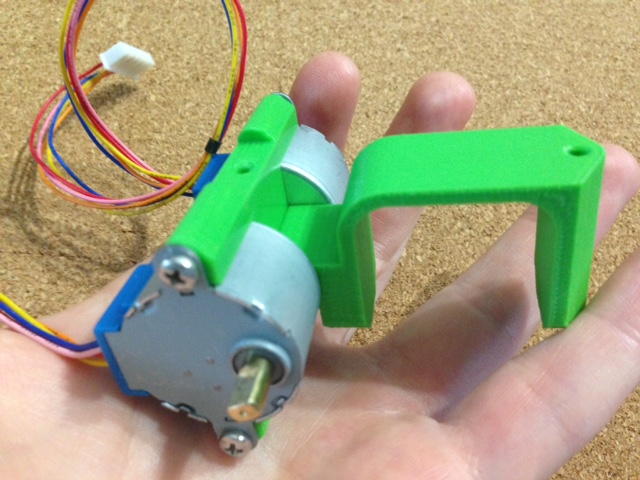
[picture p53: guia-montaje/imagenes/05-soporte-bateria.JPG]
05-soporte-bateria


## Soporte placa botonera

Material necesario:
* *Pieza Addon-KeypadBracket-PCB (Ya que estoy utilizando la [placa de XDeSIG](https://github.com/pablorubma/escornabot-DIY#212-versi%C3%B3n-de-xdesig), si fabricamos la [placa totalmente artesanal](https://github.com/pablorubma/escornabot-DIY#211-placa-original-totalmente-artesanal) necesitaremos la pieza Addon-KeypadBracket-5Buttons)*
* *1 Tornillo M3 de 10mm*

>__NOTA: Pondremos solamente el tornillo de la parte trasera como puedes ver en las imágenes__

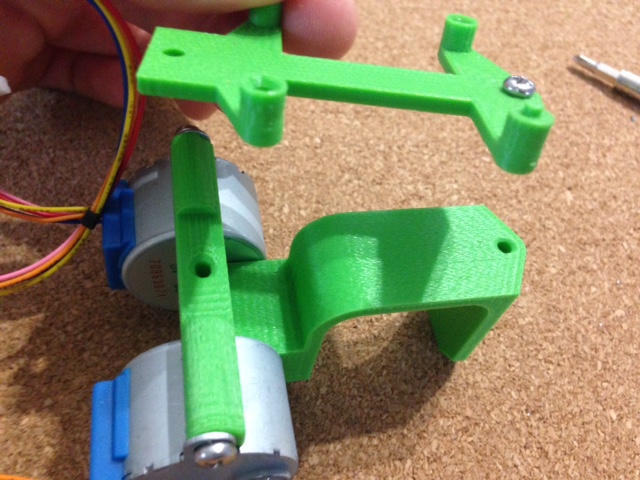
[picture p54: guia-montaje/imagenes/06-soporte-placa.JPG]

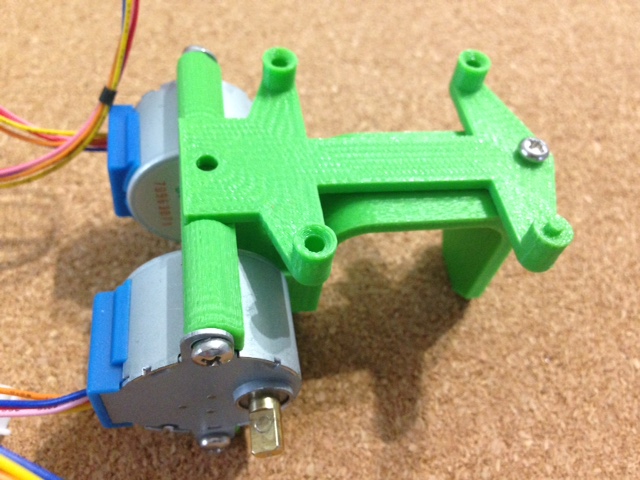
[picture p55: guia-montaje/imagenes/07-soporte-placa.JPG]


## Soporte protoboard 170 puntos

Material necesario:
* *Pieza "board-bracket"*
* *2 Tornillos M3 de 10mm*

>__NOTA: La pieza se encaja encima del soporte de la placa botonera y lleva otro tornillo en la parte inferior de los motores (Yo no suelo poner este tornillo porque me queda fijo solo con el superior)__

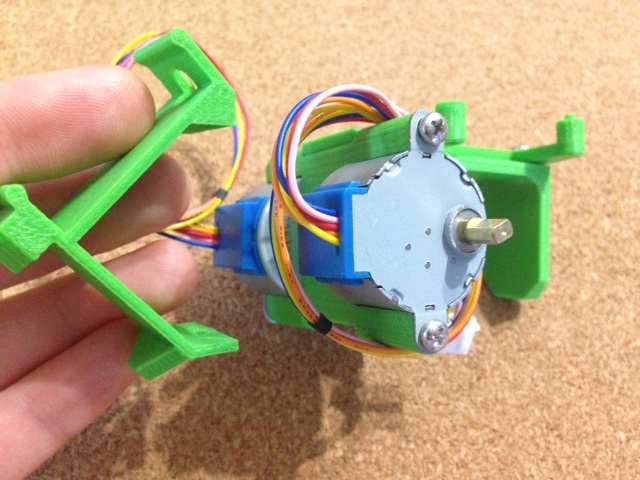
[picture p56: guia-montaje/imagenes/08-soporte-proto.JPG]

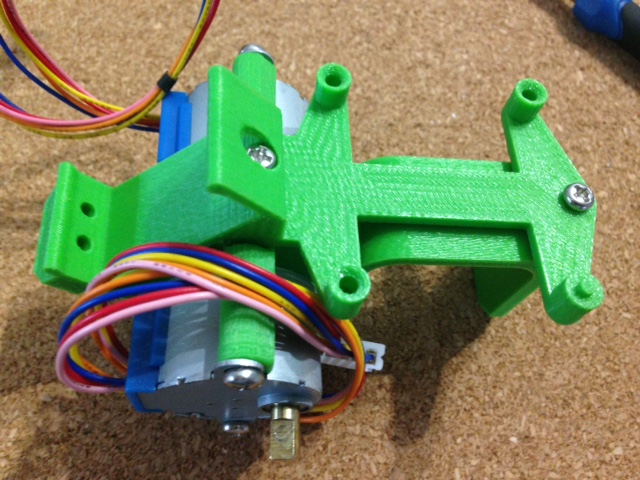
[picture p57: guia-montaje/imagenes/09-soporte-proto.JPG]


## Portapilas y bola

Material necesario:
* *Pieza "ballcaster-v2"*
* *2 Tornillos M3 de 10mm*
* *Bola o canica de 14mm*
* *Portapilas AA"
* *4 Pilas AA*

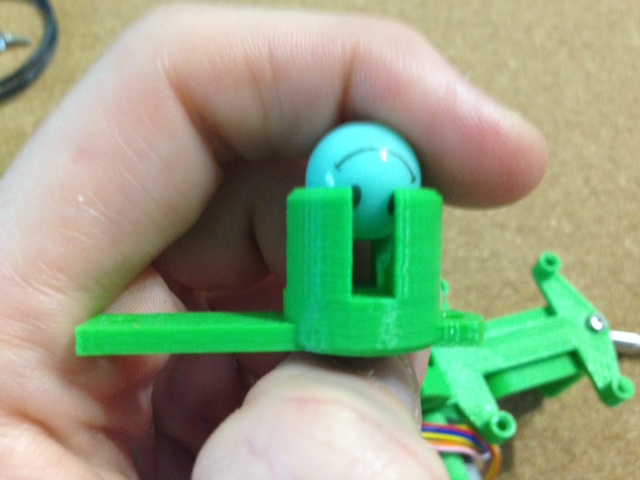
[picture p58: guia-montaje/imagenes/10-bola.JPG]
  
>__NOTA BOLA: Puede que la bola se salga, lo puedes solucionar calentando un poco la pieza y ajustando al gusto (con cuidado ^_^).__  

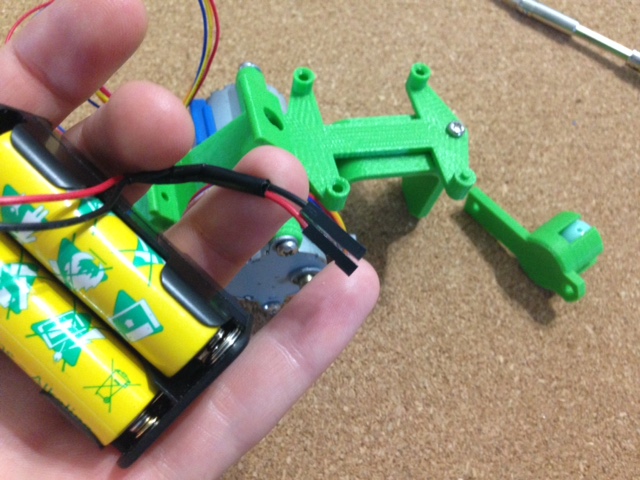
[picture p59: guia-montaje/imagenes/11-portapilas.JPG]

>__NOTA PORTAPILAS: En algunos modelos tienen una posición concreta en la que encajan para no forzar la pieza donde va colocado. No utilizo interruptor, así que empalmo unos terminales hembra para después pinchar en la protoboard (puedes ponerlo de otro modo si quieres ^_^)__  

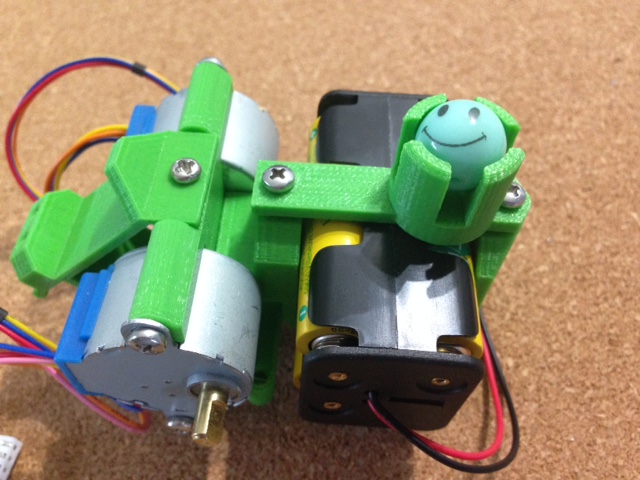
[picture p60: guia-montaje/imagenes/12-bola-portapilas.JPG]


>__NOTA PORTAPILAS: Si ves la siguiente imagen en este modelo queda una separación entre las dos piezas y se aprecia un trozo de tornillo. No hace falta ajustar los tornillos a dolor porque te puedes cargar alguna pieza, es suficiente si ajusta y no se mueve.__

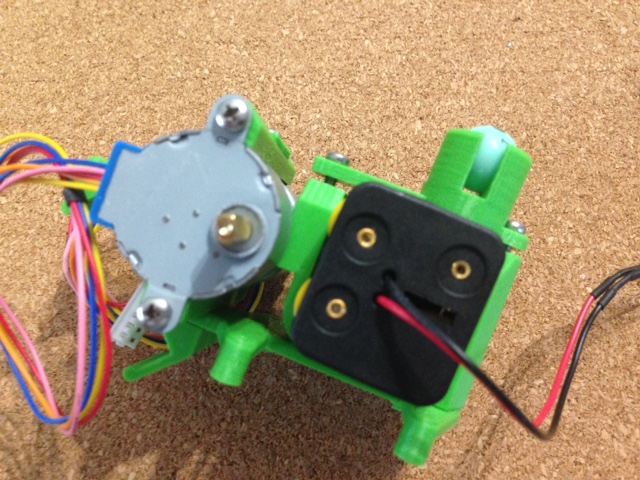
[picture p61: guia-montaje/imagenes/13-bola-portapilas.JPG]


## Protoboard 170 puntos

Material necesario:
* *Protoboard*

>__NOTA: Al colocar encima el Arduino NANO dejo tres hileras libres en la parte superior y dos en la parte inferior. El único misterio de la protoboard es como todo en la vida, encajarla con cariño ^_^.__

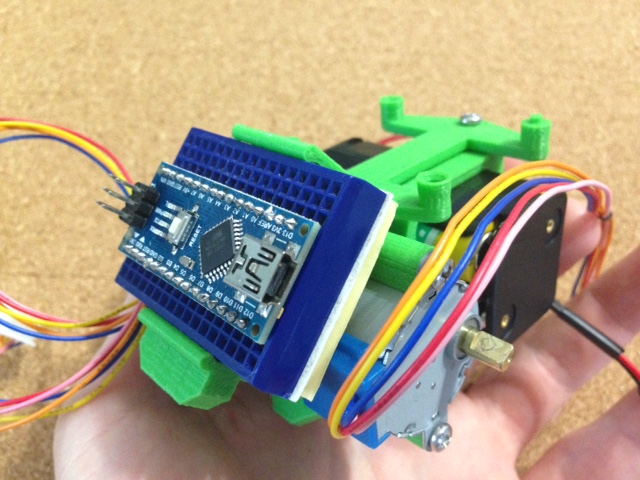
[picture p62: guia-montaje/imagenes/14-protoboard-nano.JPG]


## Drivers para controlar los motores

### Colocación de los drivers

Material necesario:
* *2 Drivers ULN2003*
* *2 Tornillos M3 de 10mm (Puedes usar más corticos)*

>__NOTA: Mira en la siguiente imagen como va colacada la placa o te pegará después con las ruedas. Los cuatro pines macho tienen que ir en la parte superior.__

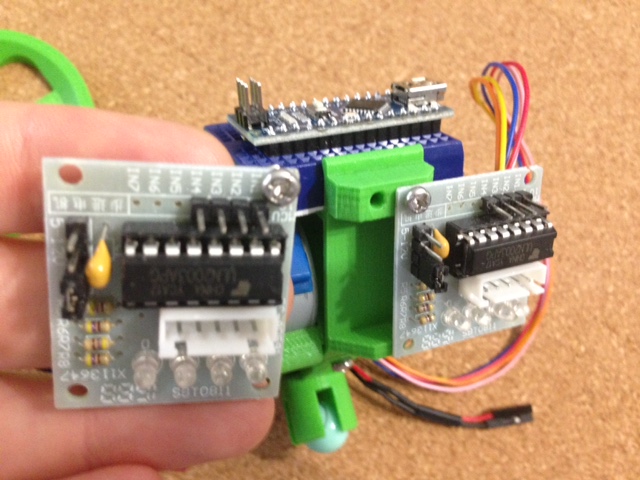
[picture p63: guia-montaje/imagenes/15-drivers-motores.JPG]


>__NOTA: el de la izquierda (mirando la imagen) te quedará un poquito torcido porque pegarán las soldaduras de la parte trasera en la pieza impresa3D.__

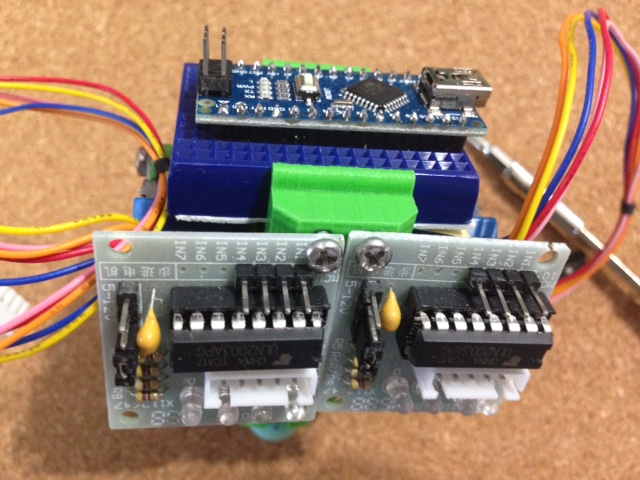
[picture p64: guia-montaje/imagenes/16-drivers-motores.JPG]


>__NOTA: Un truco para que los cables queden recogidos es pasar el cable por el driver contrario tal y como puedes ver en la siguiente imagen.__

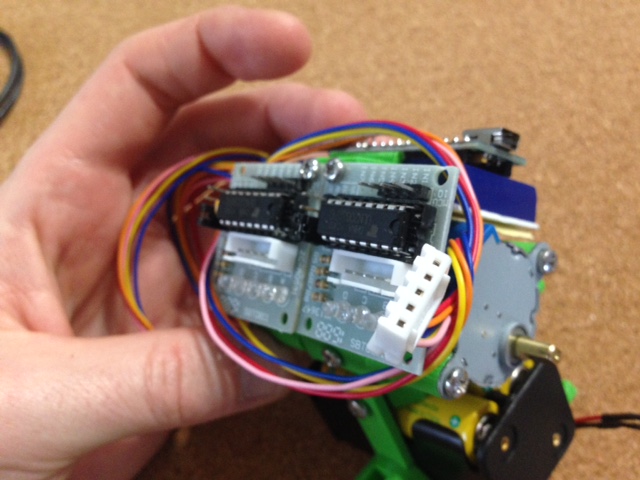
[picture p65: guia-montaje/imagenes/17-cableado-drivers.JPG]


### Colocación cableado de los drivers-protoboard

Puedes consultar la [guía de cableado en la web escornabot](https://escornabot.com/web/es/content/cableado) si te quedas con dudas

Material necesario:
* *8 cables arduino macho-hembra de 10cm (me gusta usar de colores pero puedes usar los que quieras)*
* *2 cables arduino macho-hembra de 10cm negros (puedes usar de otro color)*
* *2 cables arduino macho-hembra de 10cm rojos (puedes usar de otro color)*

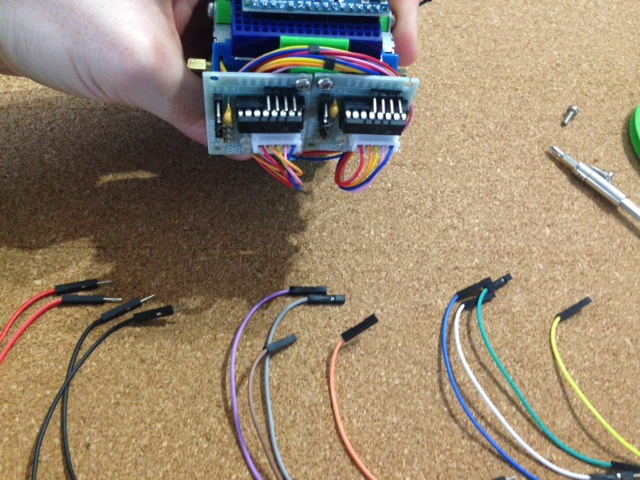
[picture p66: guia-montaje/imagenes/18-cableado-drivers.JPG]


>__NOTA: La conexión es fácil, "mirando de frente los drivers" empezamos por los cuatro conectores de arriba, primero el de arriba a la derecha lo pinchamos en el pin D9 y los otros tres a continuación en orden D8, D7, D6.__

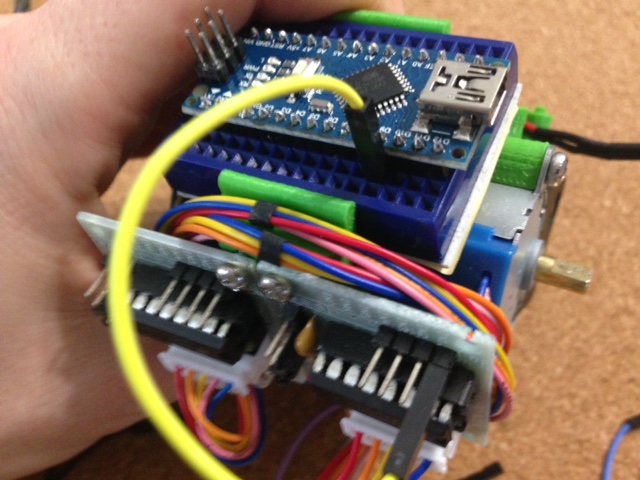
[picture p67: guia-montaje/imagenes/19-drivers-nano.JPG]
  
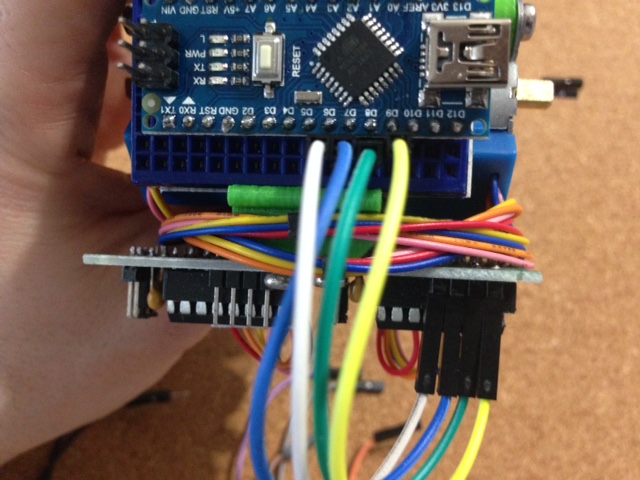
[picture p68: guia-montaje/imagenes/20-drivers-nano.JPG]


>__NOTA: Ahora a por el de la izquierda "mirando de frente los drivers" los conectaremos a continuación D5, D4, D3 y D2__

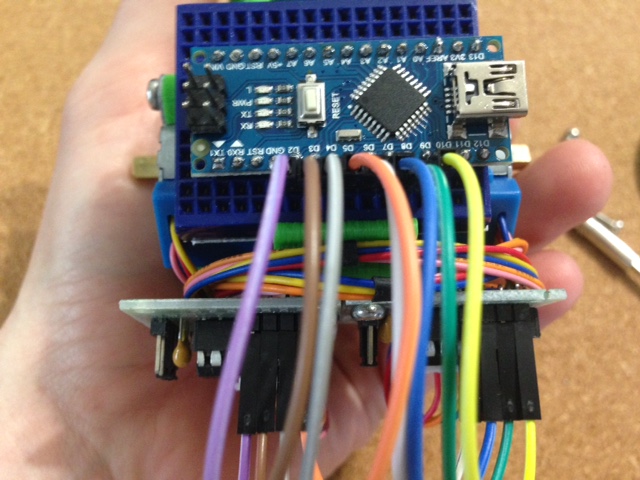
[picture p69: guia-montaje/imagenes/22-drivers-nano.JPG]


>__NOTA: Vamos a conectar positivo y negativo. Lo tienes marcado en el driver. En este caso el de abajo positivo, el de arriba negativo. Positivo va colocado al pin VIN y el Negativo a GND__

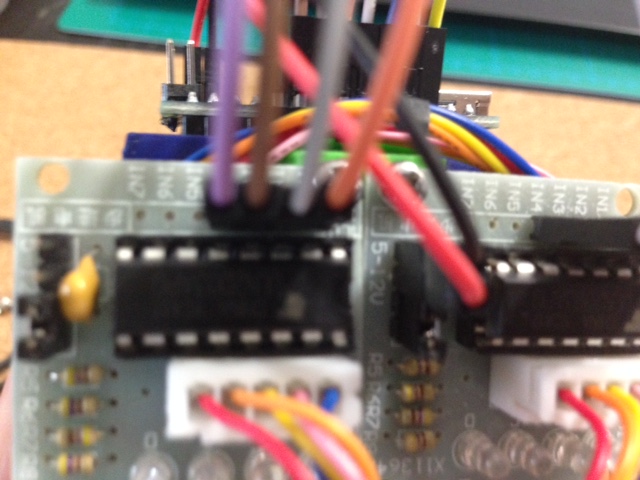
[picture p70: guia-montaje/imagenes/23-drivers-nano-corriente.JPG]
  
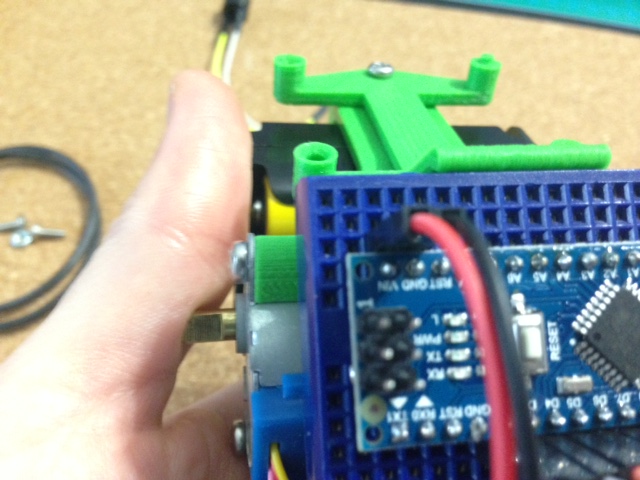
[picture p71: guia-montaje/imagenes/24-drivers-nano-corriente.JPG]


>__NOTA: El resultado final debería ser algo así :P__

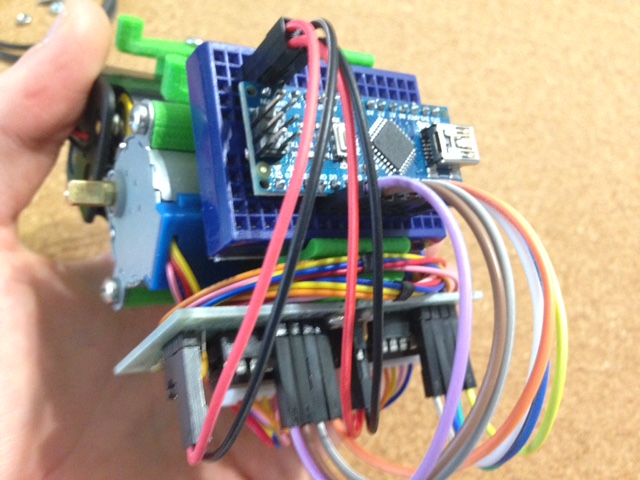
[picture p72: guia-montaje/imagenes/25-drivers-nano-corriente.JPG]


## Placa botonera

Material necesario:
* *Placa botonera (da igual si usas [placa de XDeSIG](https://github.com/pablorubma/escornabot-DIY#212-versi%C3%B3n-de-xdesig) o la [placa totalmente artesanal](https://github.com/pablorubma/escornabot-DIY#211-placa-original-totalmente-artesanal))*
* *3 Cables arduino macho-hembra de 10cm*

>__IMPORTANTE: Primero realiza el Test de la botonera, tienes todos los pasos a seguir en la guía [comprobación y configuración de las lecturas de la botonera](https://escornabot.com/web/es/content/comprobacion-y-configuracion-de-las-lecturas-de-botonera)__

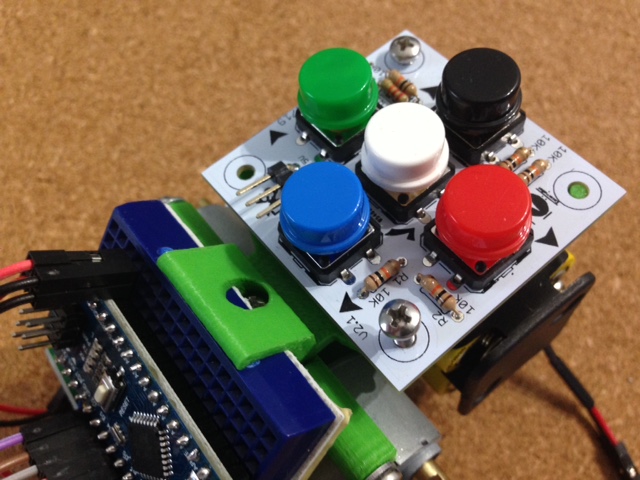
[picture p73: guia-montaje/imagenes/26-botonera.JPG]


>__NOTA: El pin cercano al botón azul es GND, lo coloco en el GND de la parte inferior.  
El pin central es la conexión de datos, lo coloco en el pin A4 (recuerda revisar el código después para ver que tienes configurado el teclado en este pin).  
El pin exterior es el positivo y lo conectaremos al pin de 5V (en el caso de no ir arcado en el Arduino NANO, tienes que dejar un hueco de separación con GND)__

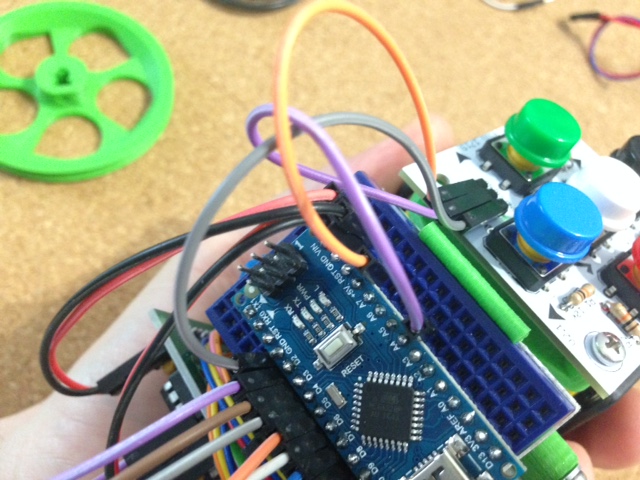
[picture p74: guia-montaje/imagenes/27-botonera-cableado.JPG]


## Buzzer 5V o zumbador

Material necesario:
* *Buzzer 5V*
* *2 Cables arduino macho-hembra de 10cm (me gusta usar uno blanco para negativo y uno amarillo para positivo ^_^)*

>__NOTA: Normalmente el positivo va marcado y suele ser la patilla larga. Yo lo pongo con los cablecicos colgando porque me mola, pero aquí free-style.
Positivo lo conectamos al Pin D10 y negativo al GND que nos queda libre en la parte inferior.__

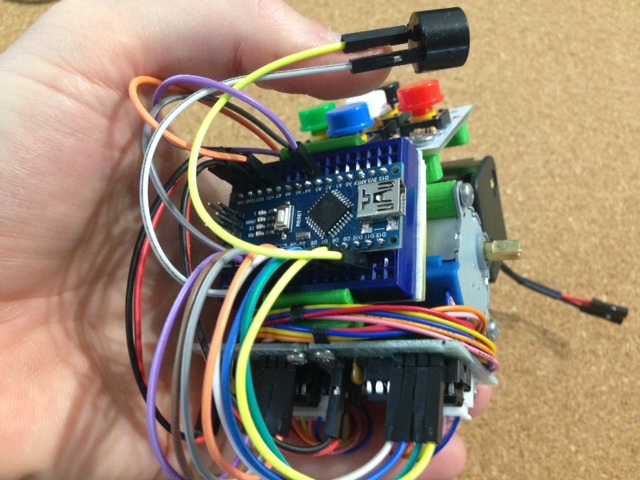
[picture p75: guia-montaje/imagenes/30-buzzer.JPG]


## Ruedas

Material necesario:
* *Pieza "wheel-l"*
* *Pieza "wheel-r"*
* *2 Juntas tóricas 63x60x3mm*
* *2 Tornillos M3 de 10mm*
* *2 Tuercas M3*

>__NOTA: La tuerca debería entrar sin forzar mucho, si ves que no encaja siempre puedes tirar de soldador calentar con cuidado y encajar. Una vez encajada coloca el tornillo sin que asome la punta por la tuerca, así después solo tienes que pretar una vez tengas la rueda montada__

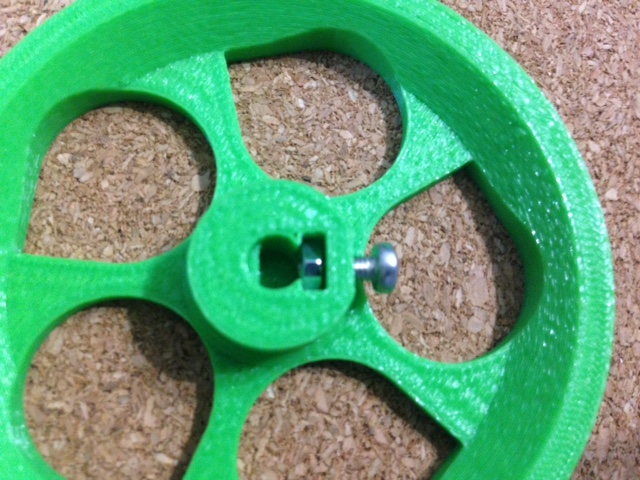
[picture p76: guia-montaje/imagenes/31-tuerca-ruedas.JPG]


>__NOTA: La junta dependiendo del tamaño te costará un poco ponerla pero no hay mayor problema__

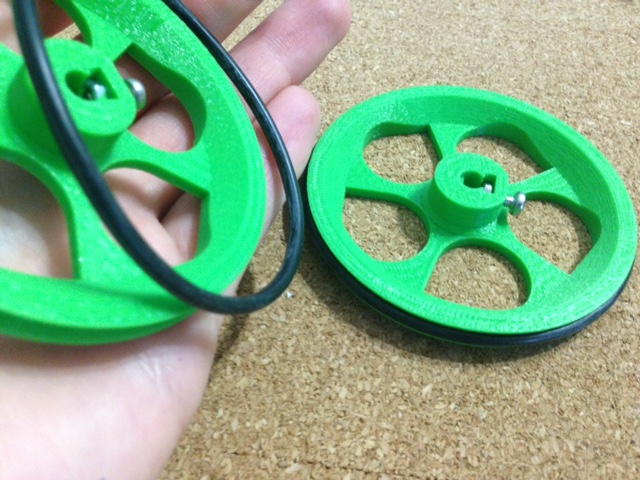
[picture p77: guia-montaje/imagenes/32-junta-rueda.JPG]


>__NOTA: La rueda lleva la forma del engancha con el motor. Una vez puesta, mueve la rueda para que el tornillo te quede en la parte inferior y lo puedas ajustar con facilidad.__

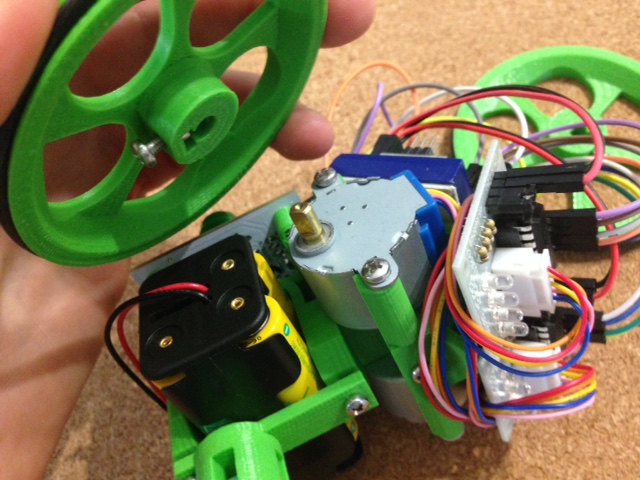
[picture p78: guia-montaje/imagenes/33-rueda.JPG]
  
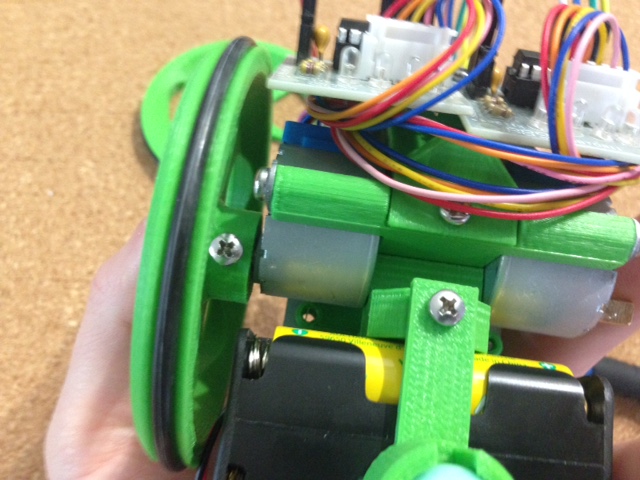
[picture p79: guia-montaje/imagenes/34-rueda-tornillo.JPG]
  

## Conexión cables corriente pilas

Material necesario:
* *2 Cables arduino macho-macho 10cm*  

*Lo repito, a mi me gusta montarlo así. Puedes ponerle un interruptor o lo que quieras :P*  

>__NOTA: Si has dejado tres huecos en la hilera superior como dije al inicio te quedará sitio para poner el positivo en VIN y negativo en GND como puedes ver en la foto.__  

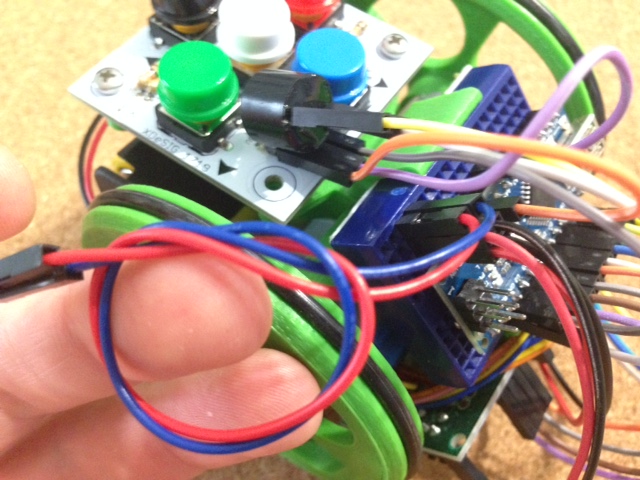
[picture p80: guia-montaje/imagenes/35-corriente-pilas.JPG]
  

## Carga el código Arduino  

Solo te quedará cargar el código, lo tienes explicado [aquí](https://github.com/pablorubma/escornabot-DIY#5-instalaci%C3%B3n-ide-arduino-y-descarga-de-la-programaci%C3%B3n)  

# Conecta los cables de corriente con los del portapilas y a JUGAR!!  

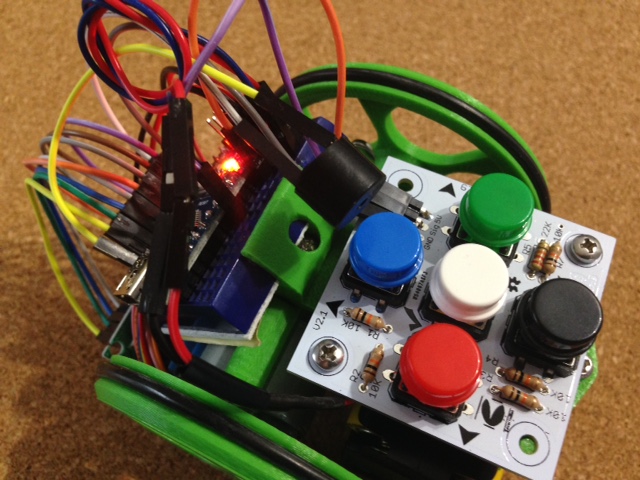
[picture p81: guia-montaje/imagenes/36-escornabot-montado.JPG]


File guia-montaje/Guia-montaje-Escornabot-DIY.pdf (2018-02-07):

# GUÍA MONTAJE ESCORNABOT-DIY

## Visita el proyecto original escornabot.com

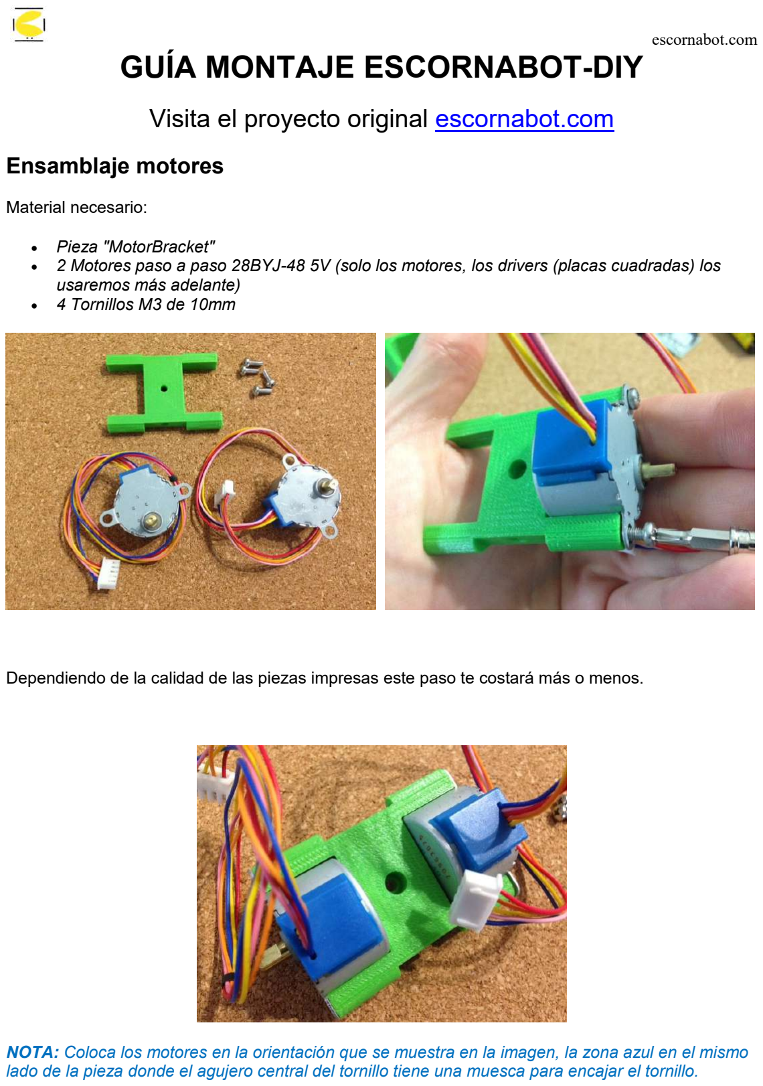
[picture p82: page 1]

escornabot.com

## Ensamblaje motores

Material necesario:

- Pieza "MotorBracket"
- 2 Motores paso a paso 28BYJ-48 5V (solo los motores, los drivers (placas cuadradas) los usaremos más adelante)
- 4 Tornillos M3 de 10mm

Dependiendo de la calidad de las piezas impresas este paso te costará más o menos.

NOTA: Coloca los motores en la orientación que se muestra en la imagen, la zona azul en el mismo lado de la pieza donde el agujero central del tornillo tiene una muesca para encajar el tornillo.

## Soporte portapilas-batería

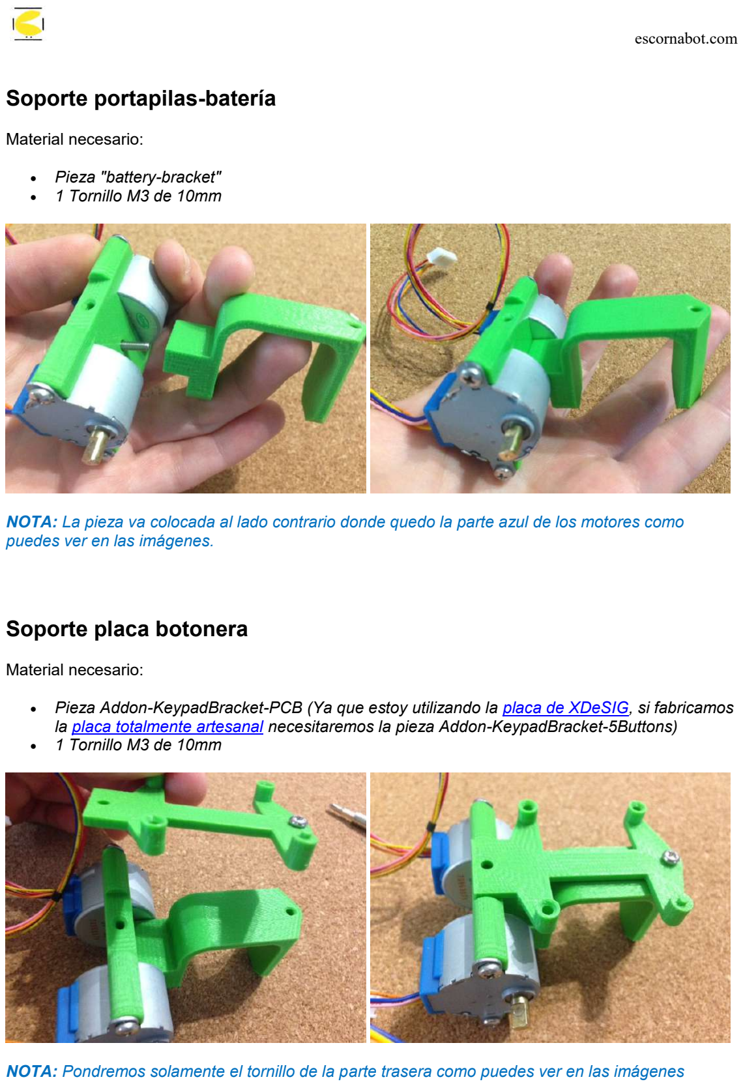
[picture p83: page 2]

Material necesario:

- Pieza "battery-bracket"
- 1 Tornillo M3 de 10mm

NOTA: La pieza va colocada al lado contrario donde quedo la parte azul de los motores como puedes ver en las imágenes.

## Soporte placa botonera

Material necesario:

- Pieza Addon-KeypadBracket-PCB (Ya que estoy utilizando la placa de XDeSIG, (https://github.com/pablorubma/escornabot-DIY#212-versi%C3%B3n-de-xdesig) si fabricamos la placa totalmente artesanal (https://github.com/pablorubma/escornabot-DIY#211-placa-original-totalmente-artesanal) necesitaremos la pieza Addon-KeypadBracket-5Buttons)
- 1 Tornillo M3 de 10mm

NOTA: Pondremos solamente el tornillo de la parte trasera como puedes ver en las imágenes

## Soporte protoboard 170 puntos

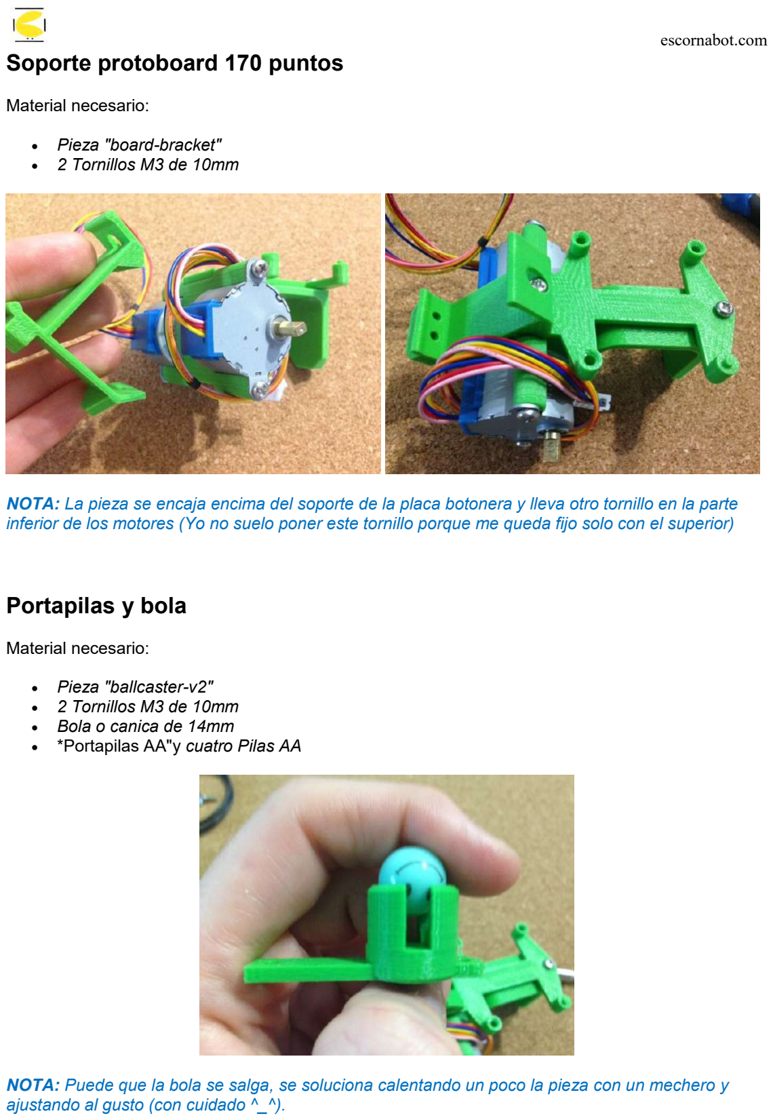
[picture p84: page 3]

Material necesario:

- Pieza "board-bracket"
- 2 Tornillos M3 de 10mm

NOTA: La pieza se encaja encima del soporte de la placa botonera y lleva otro tornillo en la parte inferior de los motores (Yo no suelo poner este tornillo porque me queda fijo solo con el superior)

## Portapilas y bola

Material necesario:

- Pieza "ballcaster-v2"
- 2 Tornillos M3 de 10mm
- Bola o canica de 14mm
- *Portapilas AA"y cuatro Pilas AA

NOTA: Puede que la bola se salga, se soluciona calentando un poco la pieza con un mechero y ajustando al gusto (con cuidado ^_^).

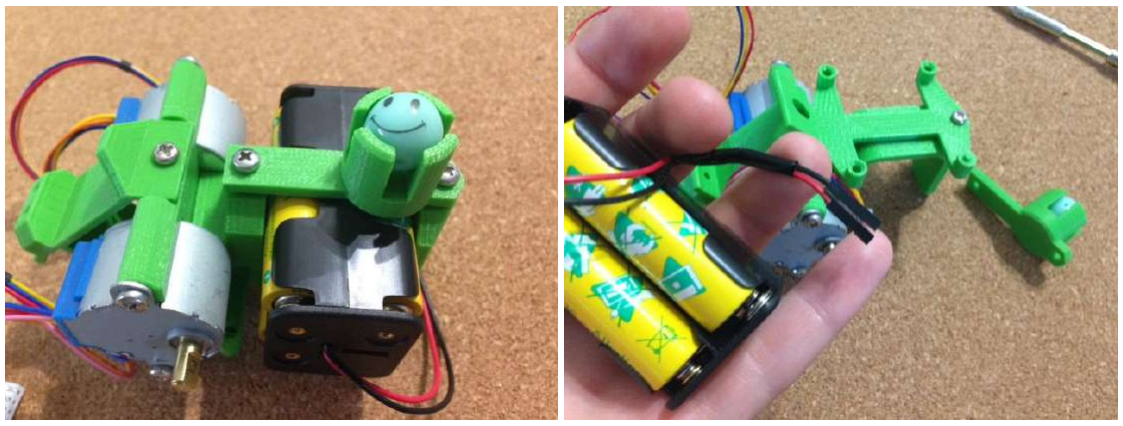
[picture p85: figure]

NOTA: En algunos modelos tienen una posición concreta en la que encajan para no forzar la pieza donde va colocado. No utilizo interruptor, así que empalmo unos terminales hembra para después pinchar en la protoboard (puedes ponerlo de otro modo si quieres ^_^)

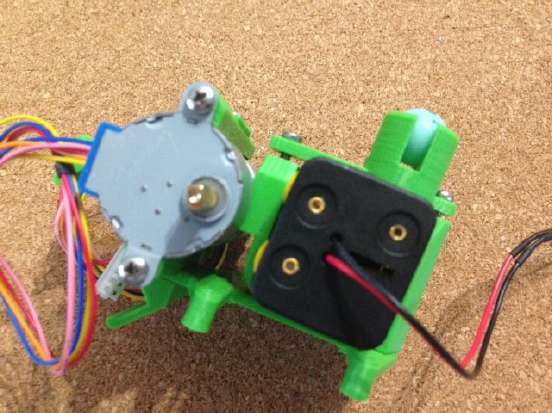
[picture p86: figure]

NOTA: Como ves en la imagen, en este modelo queda una separación entre las dos piezas y se aprecia un trozo de tornillo. No hace falta ajustar los tornillos hasta el fondo porque te puedes cargar alguna pieza, es suficiente si ajusta y no se mueve.

## Protoboard 170 puntos

Material necesario:

- Protoboard

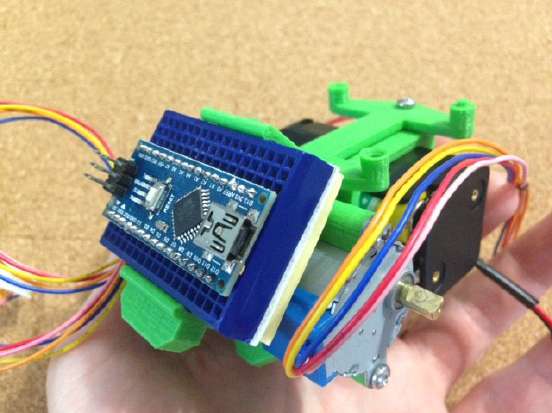
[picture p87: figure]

NOTA: Al colocar encima el Arduino NANO dejo tres hileras libres en la parte superior y dos en la parte inferior. El único misterio de la protoboard es como todo en la vida, encajarla con cariño ^_^.

## Drivers para controlar los motores

Colocación de los drivers

Material necesario:

- 2 Drivers ULN2003
- 2 Tornillos M3 de 10mm (Puedes usar más corticos de 5 o 6mm)

NOTA: Mira en la siguiente imagen como va colacada la placa o te pegará después con las ruedas. Los cuatro pines macho tienen que ir en la parte superior.


NOTA: el de la izquierda (mirando la imagen) te quedará un poquito torcido porque pegarán las soldaduras de la parte trasera en la pieza impresa3D.


NOTA: Un truco para que los cables queden recogidos es pasar el cable por el driver contrario empezando por la parte de abajo y rodeando los dos.

Colocación cableado de los drivers-protoboard

Puedes consultar la guía de cableado en la web escornabot (https://escornabot.com/web/es/content/cableado) si te quedas con dudas

Material necesario:

- 8 cables arduino macho-hembra de 10cm (me gusta usar de colores pero puedes usar los que quieras)
- 2 cables arduino macho-hembra de 10cm negros (puedes usar de otro color)
- 2 cables arduino macho-hembra de 10cm rojos (puedes usar de otro color)


La conexión es fácil, "mirando de frente los drivers" empezamos por los cuatro conectores de arriba, primero el de arriba a la derecha lo pinchamos en el pin D9 y los otros tres a continuación en orden D8, D7, D6.

Ahora a por el de la izquierda "mirando de frente los drivers" los conectaremos a continuación D5, D4, D3 y D2.


Vamos a conectar positivo y negativo. Lo tienes marcado en el driver. En este caso el de abajo positivo, el de arriba negativo. Positivo va colocado al pin VIN y el Negativo a GND

El resultado final debería ser algo así :P

## Placa botonera

Material necesario:

- Placa botonera (da igual si usas placa de XDeSIG (https://github.com/pablorubma/escornabot-DIY#212-versi%C3%B3n-de-xdesig) o la placa totalmente artesanal) (https://github.com/pablorubma/escornabot-DIY#211-placa-original-totalmente-artesanal)
- 3 Cables arduino macho-hembra de 10cm
- 2 Tornillos M3 de 10mm (Puedes usar más corticos de 5 o 6mm)

IMPORTANTE: Primero realiza el Test de la botonera, tienes todos los pasos a seguir en la guía comprobación y configuración de las lecturas de la botonera (https://escornabot.com/web/es/content/comprobacion-y-configuracion-de-las-lecturas-de-botonera)


El pin cercano al botón azul es GND, lo coloco en el GND de la parte inferior.

El pin central es la conexión de datos, lo coloco en el pin A4 (recuerda revisar el código después para ver que tienes configurado el teclado en este pin).

El pin exterior es el positivo y lo conectaremos al pin de 5V (en el caso de no ir marcado en el Arduino NANO, tienes que dejar un hueco de separación con GND)

## Buzzer 5V o zumbador

Material necesario:

- Buzzer 5V
- 2 Cables arduino macho-hembra de 10cm (me gusta usar uno blanco para negativo y uno amarillo para positivo ^_^)

Normalmente el positivo va marcado y suele ser la patilla larga. Yo lo pongo con los cablecicos colgando porque me mola, pero aquí free-style. Positivo lo conectamos al Pin D10 y negativo al GND que nos queda libre en la parte inferior.

## Ruedas

Material necesario:


- Pieza "wheel-l" y pieza "wheel-r"
- 2 Juntas tóricas 63x60x3mm
- 2 Tornillos M3 de 10mm y 2 Tuercas M3

La tuerca debería entrar sin forzar mucho, siempre puedes usar el soldador para encajarla pero con mucho cuidado. Después coloca el tornillo sin que asome la punta por la tuerca, así después solo tienes que apretar una vez tengas la rueda montada.


La junta tórica dependiendo del tamaño te costará un poco ponerla pero no hay mayor problema

NOTA: La rueda lleva la forma del engancha con el motor.

Mueve la rueda para que el tornillo te quede en la parte inferior y lo puedas ajustar con facilidad.

## Conexión cables corriente pilas

Material necesario:

- 2 Cables arduino macho-macho 10cm

Lo repito, a mi me gusta montarlo así. Puedes ponerle un interruptor o lo que quieras :P

Si has dejado tres huecos en la hilera superior como dije al inicio te quedará sitio para poner el positivo en VIN y negativo en GND como puedes ver en la foto.


## Carga el código Arduino

Solo te quedará cargar el código, lo tienes explicado aquí (https://github.com/pablorubma/escornabot-DIY)

# Conecta los cables de corriente con los del portapilas y a JUGAR!!

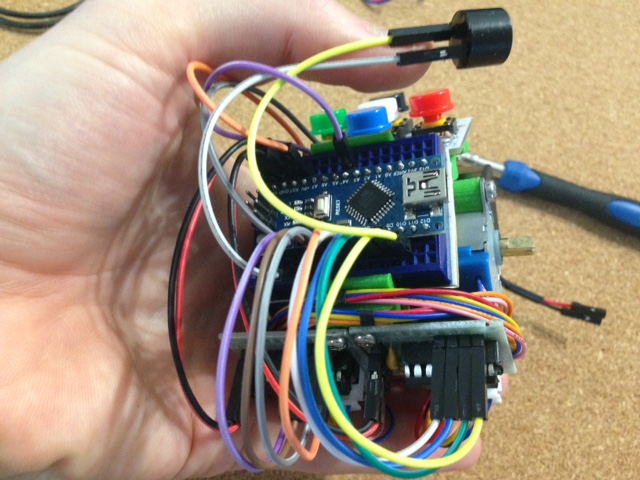
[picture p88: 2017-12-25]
guia-montaje/imagenes/29-buzzer.JPG

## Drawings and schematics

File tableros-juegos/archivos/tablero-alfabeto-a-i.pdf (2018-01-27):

# alfabeto infantil

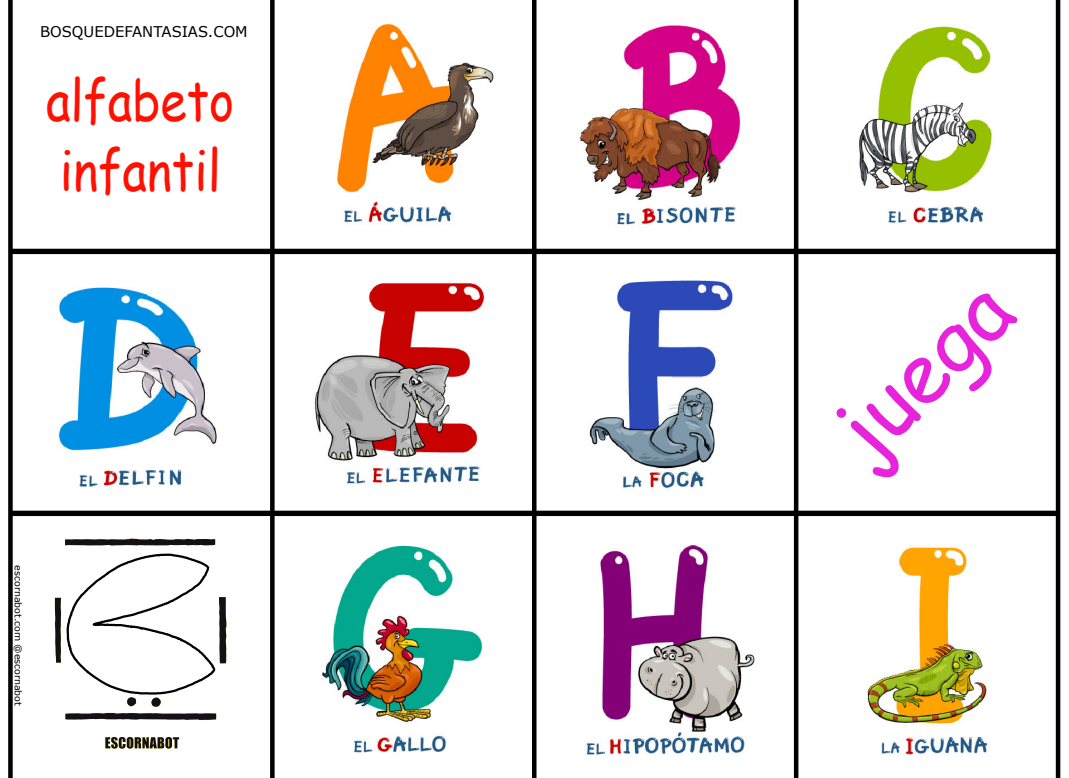
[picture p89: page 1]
BOSQUEDEFANTASIAS.COM; juega

escornabot.com @escornabot

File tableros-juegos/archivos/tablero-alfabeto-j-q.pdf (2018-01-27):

# alfabeto infantil

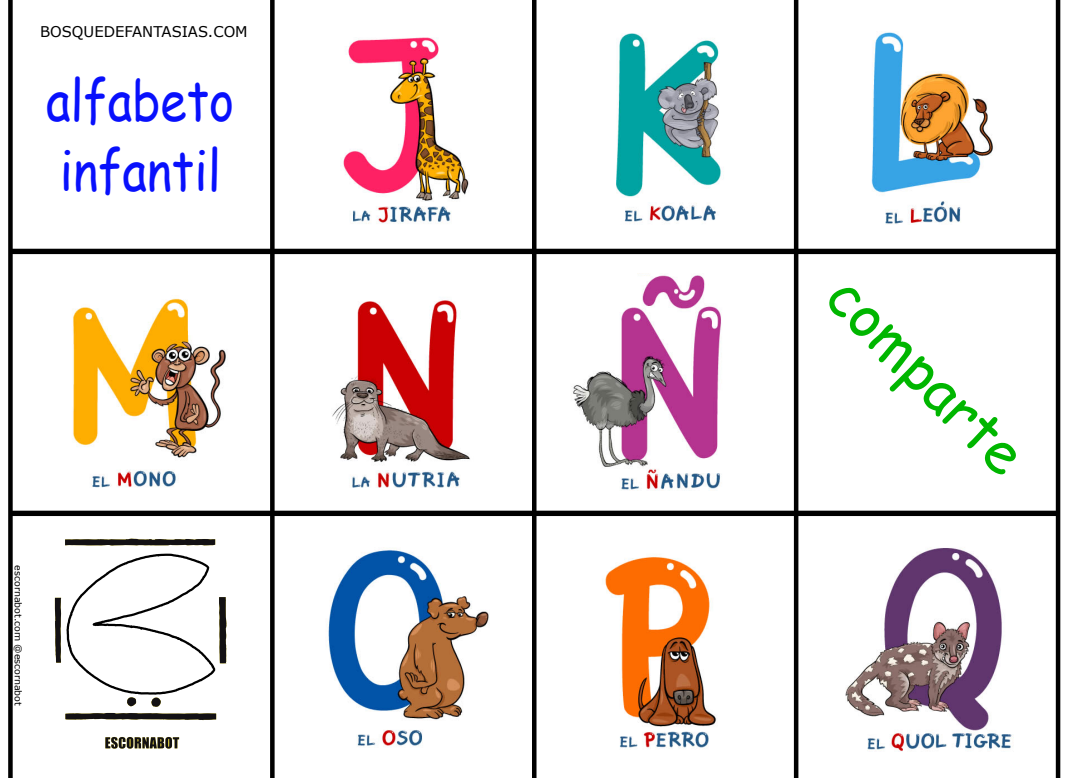
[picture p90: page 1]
BOSQUEDEFANTASIAS.COM; comparte

escornabot.com @escornabot

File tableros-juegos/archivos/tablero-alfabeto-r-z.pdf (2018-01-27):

# alfabeto infantil

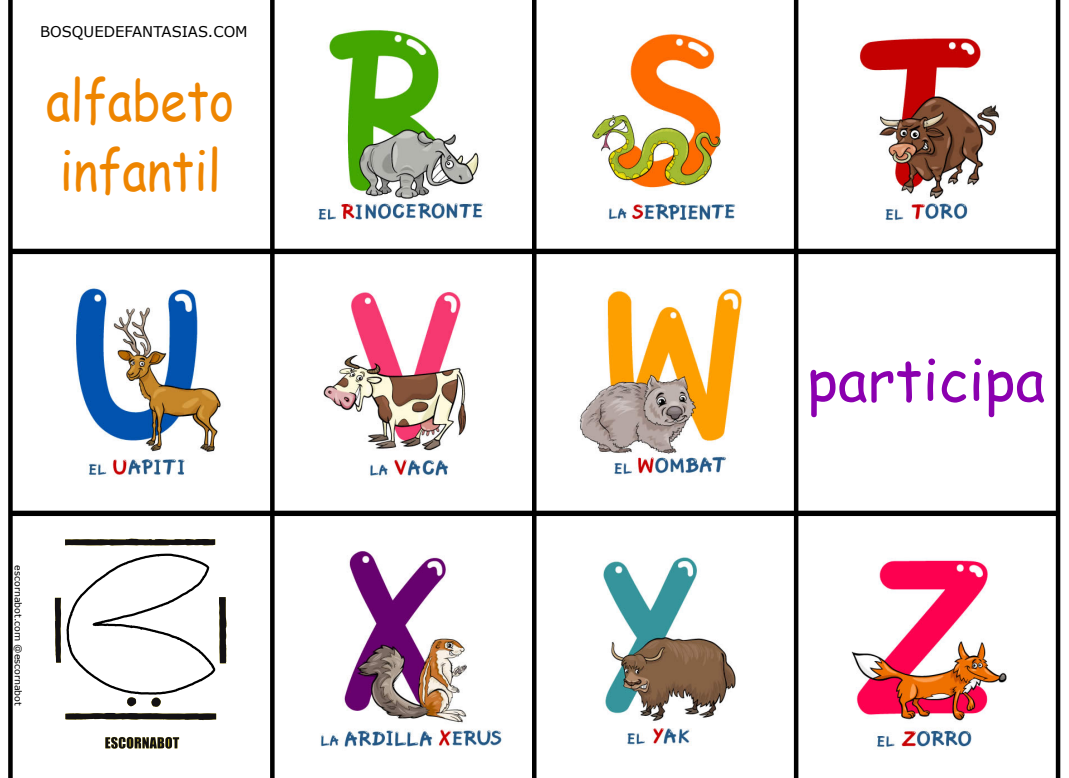
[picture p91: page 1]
BOSQUEDEFANTASIAS.COM; participa

escornabot.com @escornabot

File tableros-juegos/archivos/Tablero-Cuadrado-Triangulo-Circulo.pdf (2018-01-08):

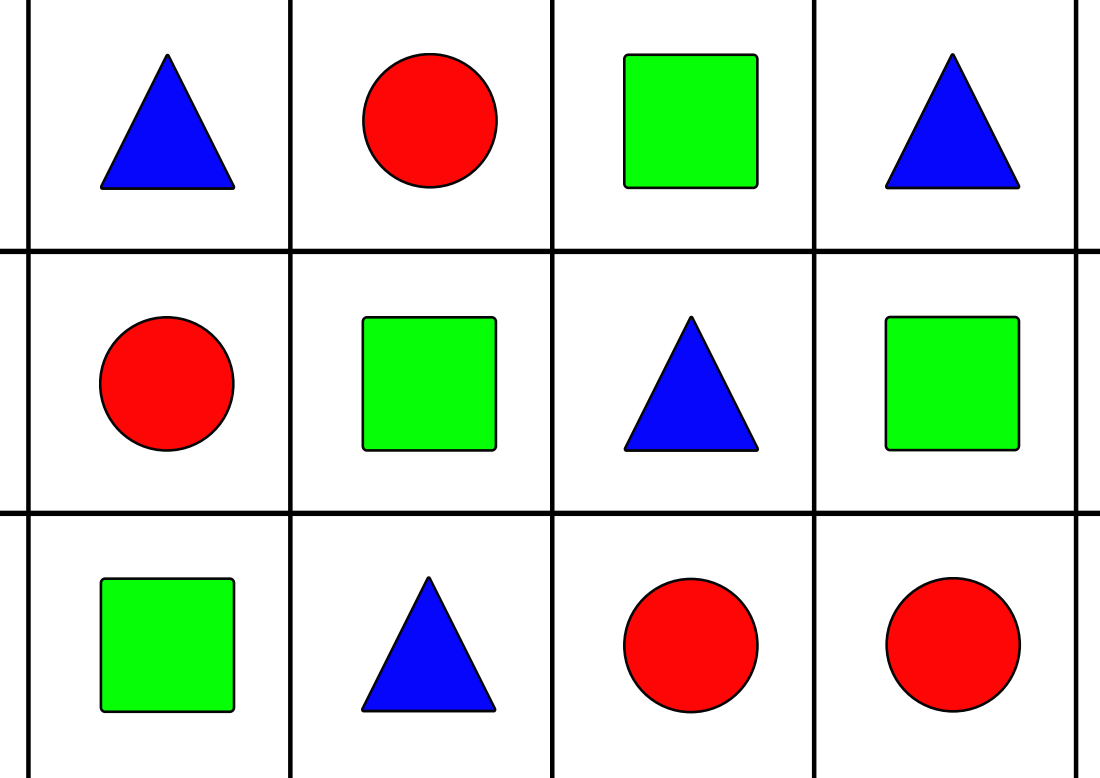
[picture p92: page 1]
Participa!; Juega!; Comparte

se trata
APRENDER
no de tener

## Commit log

2017-11-22 Create archivos-stl
2017-12-10 Update README.md
    Actualización con pasos para el montaje
2017-12-10 Delete BallCaster.stl
    Pieza anticuada
    [BallCaster.stl]
2017-12-10 Delete motor-bracket.stl
    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
    [motor-bracket.stl]
2017-12-10 Delete WheelNG.stl
    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
    [WheelNG.stl]
2017-12-25 Create README.md
    Readme inicial con el texto
2017-12-25 Create imagenes
    Crear carpeta para imágenes
2017-12-25 Create imagenes
    carpeta imágenes para la guía
2017-12-28 Update README.md
    Readme componentes - Actualizadar llegada botones, buzzer, cables y resistencias
2017-12-29 Update README.md
    Disfraces - Añadir diseños caretas para impresión 3D Lobotic
2017-12-29 Add files via upload
    Tableros-juegos. Subir las imágenes en la carpeta
2017-12-29 Update README.md
    Guía-Montaje. Actualización hasta conexión cableado drivers
2018-01-20 Create README.md
    Crear carpeta para piezas corte laser
2018-01-20 Create README.md
    Crear carpeta para piezas corte láser escornabot
2018-01-20 Add files via upload
    Piezas corte láser - Subir archivos svg piezas escornabot para corte láser
2018-01-26 Create README.md
    Carpeta para subir archivos tablero piezas tetris
2018-01-27 Update README.md
    editar formato de visualización de los tableros y añadir tableros alfabeto
2018-01-29 Update README.md
    Actualizar enlace juntas tóricas para poner las buenas
2018-02-03 Add files via upload
    Subir pieza en H para encajes
    [Pieza-H.stl]
2018-02-07 Update README.md
    Agregar pines acodados y tornillos M3 de 5mm
2018-02-08 Update README.md
    Corregir error en la descripción de las juntas tóricas
